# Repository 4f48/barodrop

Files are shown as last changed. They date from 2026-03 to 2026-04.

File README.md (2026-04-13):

# barodrop
A battery-powered, barometer-driven release system that automatically drops a payload at a configurable target altitude.

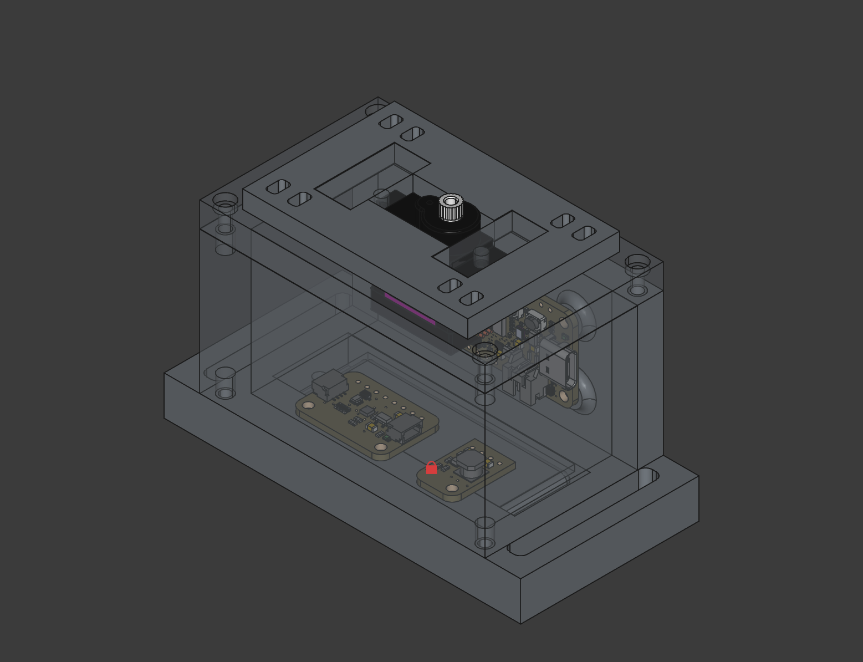
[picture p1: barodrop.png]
barodrop full assembly 3D model


## Why?
I've been participating in the Hungarian CanSat competition for two years. In my time working on the model satellite, we launched prototypes 4 times on high altitude weather balloons for testing. A key piece in these tests is the release system: it drops the CanSat before it flies too far away, making recovery marginally more difficult. However, the release system was always a pain point. Difficult to set up, integrate into existing systems' code or unreliable.

I decided to build something that solves all of these problems:

- independent electronics, keeping complexity low
- separate power supply: no battery drain
- reliability: built around a "drop plate" design
- easy setup, effortless configuration, solid construction

## Usage
Using barodrop is easy. Here's how it's done:

1. Write your desired configuration (altitude, timeout) to a microSD card and insert it into the main board.
2. Hold the flyaway part in place in order for the servo to lock it in place.
3. Plug in the battery to power on the system while holding the flyaway part.
4. Screw in the side panel.
5. You are ready to launch!

## Assembly
So you want one of these for yourself? The following guide will walk you through building it step-by-step.

### 1. Components
You'll have to source some components to build barodrop. You can find everything needed in the table below. I included the links for where I got the components.

| Component | Description | Link |
|---|---|---|
| Adafruit Feather RP2040 Adalogger | main board | [Mouser](https://mou.sr/4baPHUJ) |
| Adafruit BMP390 | barometer | [Mouser](https://mou.sr/4uvOA9I) |
| Adafruit MiniBoost 5V | booster | [Mouser](https://mou.sr/4diH9MU) |
| Tower Pro MG90S | servo motor | [HESTORE](https://www.hestore.hu/prod_10048104.html#) |
| JST PH 2-pin cable | battery cable | [Mouser](https://mou.sr/4luIpPd) |
| CNC Kitchen M2x3 | threaded insert | [3DJake](https://www.3djake.com/cnc-kitchen/threaded-inserts-m2-standard)  |
| CNC Kitchen M2.5x4 | threaded insert | [3DJake](https://www.3djake.com/cnc-kitchen/threaded-inserts-m25-standard) |
| cylinder head M2, M2.5 | screws | locally sourced / [Amazon](https://www.amazon.de/-/en/FandWay-Cylinder-Hexagon-Threaded-Stainless/dp/B0F3HJHFFS?th=1) |
| Dupont Wires | jumper wires | locally sourced / [Amazon](https://www.amazon.de/-/en/Elegoo-120pcs-Multicolored-Breadboard-arduino/dp/B01EV70C78?s=industrial&th=1) |

> Any screws (with the correct sizes) and any wires you have lying around the house will do. If you do not have any, chances are you can find these at your local hardware store. I included some Amazon links for reference.

> You can find a [more detailed BOM](https://github.com/4f48/barodrop/blob/main/BOM.csv) in the repository files.

To complete the build, you need to 3D print some parts. If you do not own a 3D printer, try a print-on-demand service. Additionally, a soldering iron with a threaded insert adapter, some solder and very basic soldering skills are needed.

### 2. Print the enclosure
Get started by 3D printing the enclosure. I recommend using PETG.

STL files: [/STL](https://github.com/4f48/barodrop/tree/main/STL)  
STEP files: [/STEP](https://github.com/4f48/barodrop/tree/main/STEP)

Print each file once. The "flyaway" part needs to be reprinted with each use, since it flies away with the balloon on release.

### 3. Insert the threads
To be able to screw the different components together, you need to install threaded inserts into the 3D printed parts.

- 2x M2 threaded inserts go into the top enclosure's bottom, near the hole in the middle.
- 1x M2 threaded insert goes into battery holder
- Populate the rest of the holes with M2.5 inserts.

### 4. Solder the components
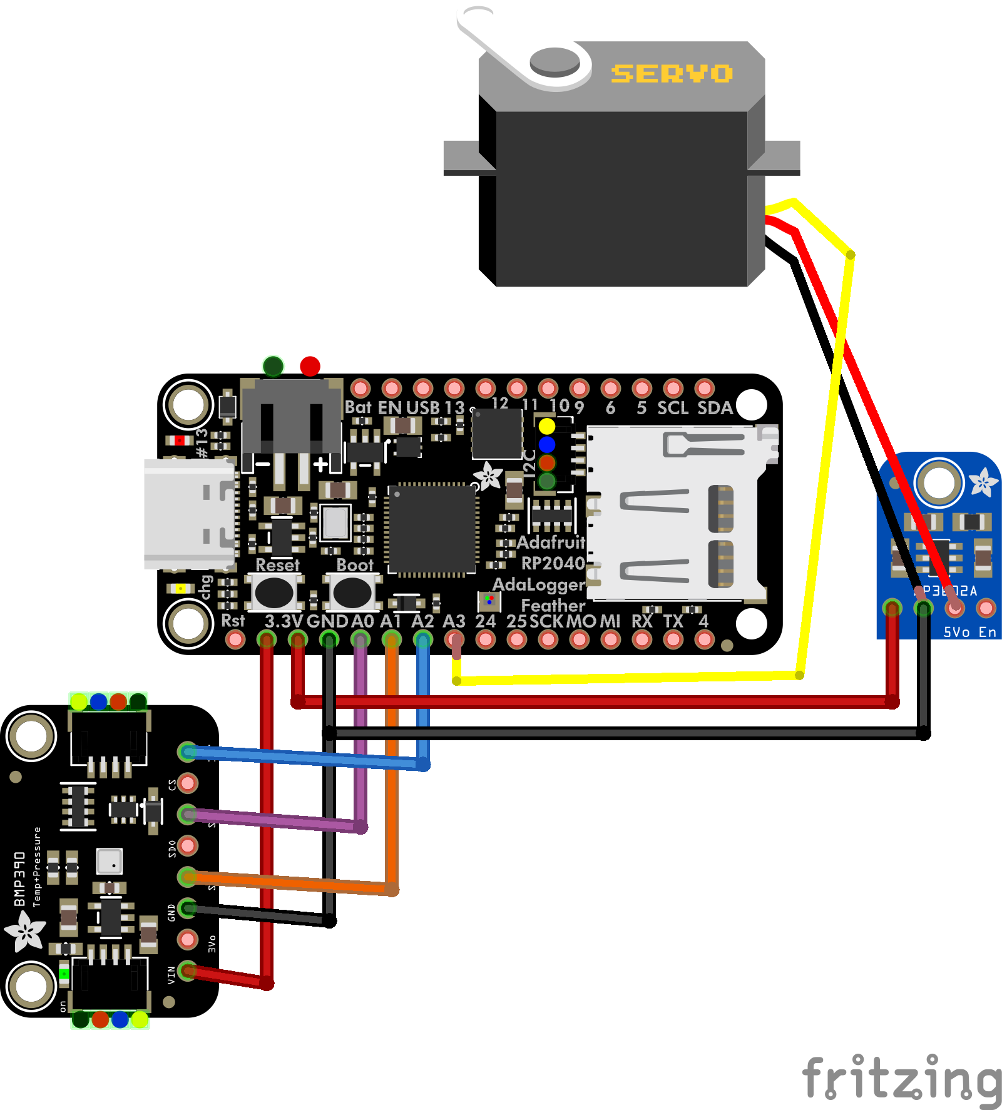
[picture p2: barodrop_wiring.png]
barodrop wiring diagram


Follow this wiring diagram to connect the components together. You might need to cut off a plug from the end of the servo's wires.

The battery comes with an incompatible connector from the factory. Cut it off, and solder on the 2-pin JST PH cable. Keep polarity in mind.

### 5. Load firmware
Firstly, download [barodrop-firmware](https://github.com/4f48/barodrop/blob/main/barodrop-firmware) from this repository.

Enter the bootloader by holding down the "Boot" button, and while continuing to hold it, press and release the "Reset" button. Keep holding the "Boot" button until the RPI-RP2 drive appears. Copy the downloaded firmware file to the RPI-RP2 drive. The RPI-RP2 drive will disappear when the firmware is loaded.

### 6. Assembly
You are almost done, we just need to put everything together. Start by placing the battery in the bottom enclosure. Cover it with the battery holder, and screw in the battery holder from the bottom. Next, mount the main board, the barometer and the booster to the bottom enclosure.

Use two M2 screws to attach the servo motor to the top enclosure. Secure the top enclosure to the bottom enclosure. Finally, screw in the side panel using two screws on the top and bottom. If you intend to power on the circuit, plug in the battery cable before screwing in the side panel.

## Bill of Materials

Download as CSV: [BOM.csv](https://github.com/4f48/barodrop/blob/main/BOM.csv)  
Download as OpenDocument Spreadsheet: [BOM.ods](https://github.com/4f48/barodrop/raw/refs/heads/main/BOM.ods)

| Component | Description | Link |
|---|---|---|
| Adafruit Feather RP2040 Adalogger | main board | [Mouser](https://mou.sr/4baPHUJ) |
| Adafruit BMP390 | barometer | [Mouser](https://mou.sr/4uvOA9I) |
| Adafruit MiniBoost 5V | booster | [Mouser](https://mou.sr/4diH9MU) |
| Tower Pro MG90S | servo motor | [HESTORE](https://www.hestore.hu/prod_10048104.html#) |
| JST PH 2-pin cable | battery cable | [Mouser](https://mou.sr/4luIpPd) |
| CNC Kitchen M2x3 | threaded insert | [3DJake](https://www.3djake.com/cnc-kitchen/threaded-inserts-m2-standard)  |
| CNC Kitchen M2.5x4 | threaded insert | [3DJake](https://www.3djake.com/cnc-kitchen/threaded-inserts-m25-standard) |
| cylinder head M2, M2.5 | screws | locally sourced / [Amazon](https://www.amazon.de/-/en/FandWay-Cylinder-Hexagon-Threaded-Stainless/dp/B0F3HJHFFS?th=1) |
| Dupont Wires | jumper wires | locally sourced / [Amazon](https://www.amazon.de/-/en/Elegoo-120pcs-Multicolored-Breadboard-arduino/dp/B01EV70C78?s=industrial&th=1) |

> Any screws (with the correct sizes) and any wires you have lying around the house will do. If you do not have any, chances are you can find these at your local hardware store. I included some Amazon links for reference.

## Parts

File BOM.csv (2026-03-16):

Part | Description | Amount | MPN | Link
Adafruit Feather RP2040 Adalogger | main board | 1 | 5980 | https://mou.sr/4baPHUJ
Adafruit BMP390 | barometer | 1 | 4816 | https://mou.sr/4uvOA9I
Adafruit MiniBoost 5V | booster | 1 | 4654 | https://mou.sr/4diH9MU
Tower Pro MG90S | servo motor | 1 | MG90S-360 | https://www.hestore.hu/prod_10048104.html
JST PH 2-pin cable | battery cable | 1 | 261 | https://mou.sr/4luIpPd
CNC Kitchen M2x3 | threaded insert | 1 | TC-M2x3,0 | https://www.3djake.com/cnc-kitchen/threaded-inserts-m2-standard
CNC Kitchen M2.5x4 | threaded insert | 1 | TC-M2,5x4 | https://www.3djake.com/cnc-kitchen/threaded-inserts-m25-standard
cylinder head M2 | screw | 3 | N/A | https://www.amazon.de/-/en/FandWay-Cylinder-Hexagon-Threaded-Stainless/dp/B0F3HJHFFS?th=1
cylinder head M3 | screw | 13 | N/A | https://www.amazon.de/-/en/FandWay-Cylinder-Hexagon-Threaded-Stainless/dp/B0F3HJHFFS?th=1
Dupont wires | jumper wires | 7 | N/A | https://www.amazon.de/-/en/Elegoo-120pcs-Multicolored-Breadboard-arduino/dp/B01EV70C78?s=industrial

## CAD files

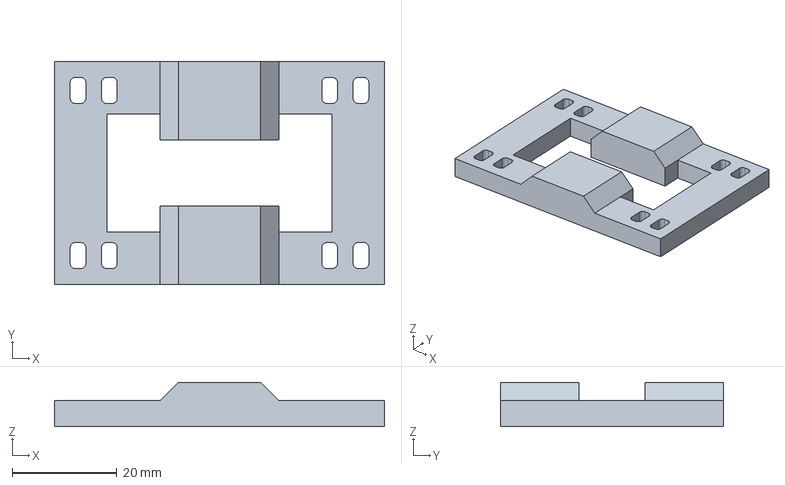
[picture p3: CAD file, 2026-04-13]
barodrop.FCStd
63.1 x 42.6 x 8.50 mm

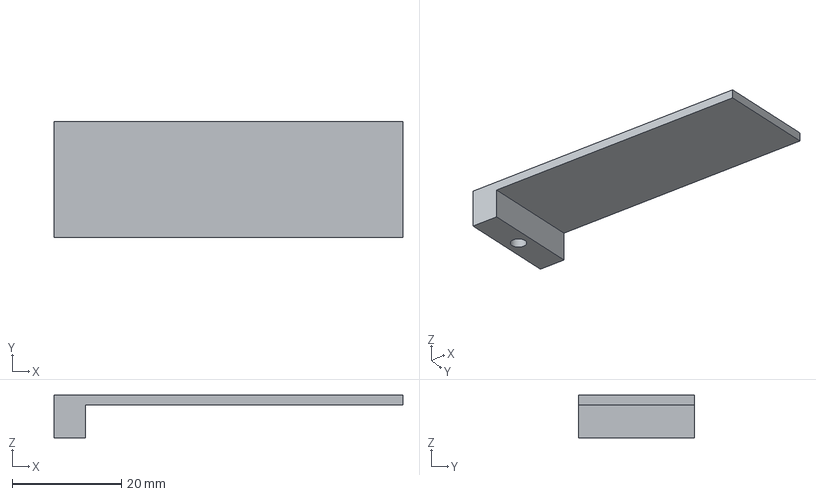
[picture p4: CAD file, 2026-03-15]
STEP/barodrop-Battery_Holder.step
63.8 x 21.2 x 7.80 mm

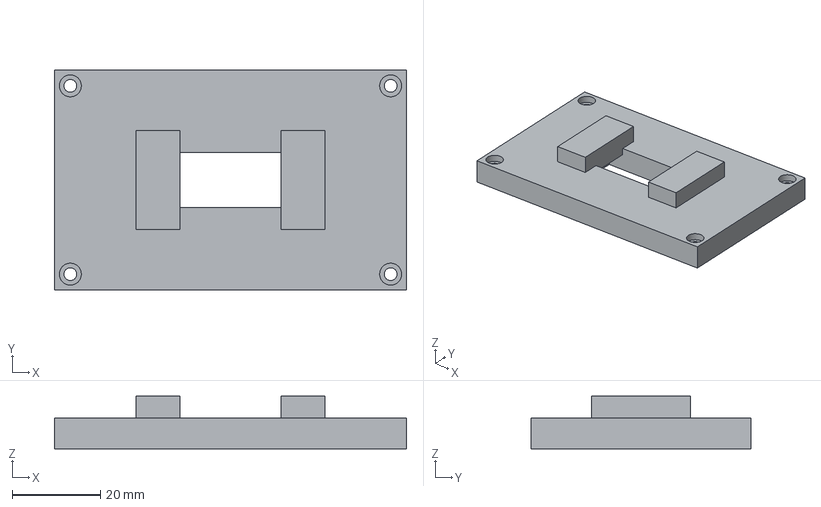
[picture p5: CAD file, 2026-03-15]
STEP/barodrop-Enclosure_Top.step
80.0 x 50.0 x 12.0 mm

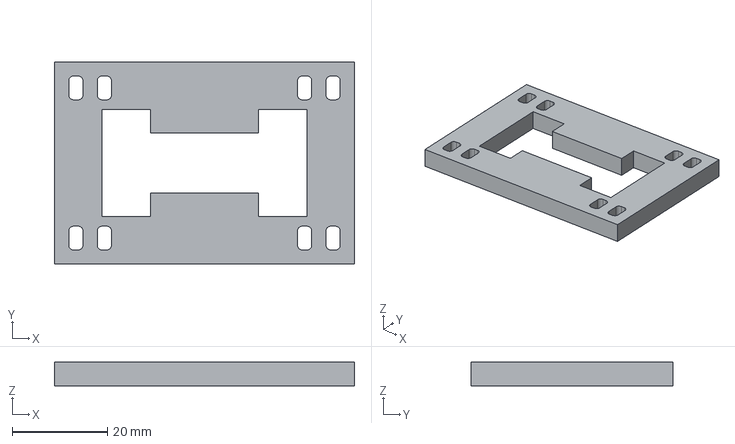
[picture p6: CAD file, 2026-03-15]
STEP/barodrop-Flyaway.step
63.1 x 42.6 x 5.00 mm

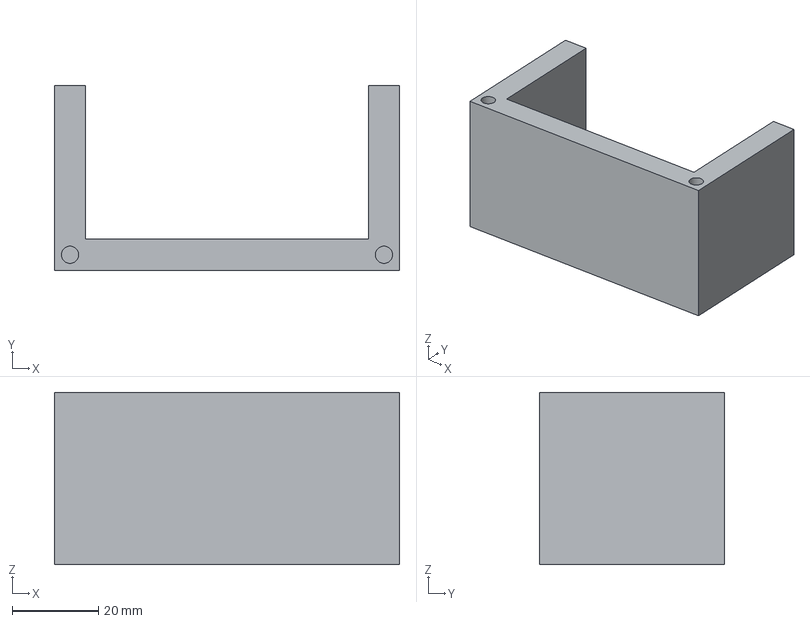
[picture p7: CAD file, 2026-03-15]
STEP/barodrop-Enclosure_Side.step
80.0 x 42.8 x 39.9 mm

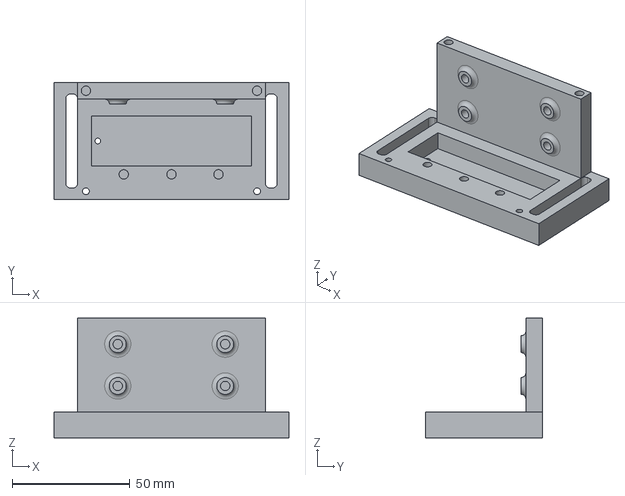
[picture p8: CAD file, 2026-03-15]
STEP/barodrop-Enclosure_Bottom.step
100.0 x 50.0 x 51.0 mm

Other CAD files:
STL/barodrop-Battery_Holder.stl
STL/barodrop-Enclosure_Bottom.stl
STL/barodrop-Enclosure_Side.stl
STL/barodrop-Enclosure_Top.stl
STL/barodrop-Flyaway.stl

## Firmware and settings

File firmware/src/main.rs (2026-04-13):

#![no_std]
#![no_main]

use bmp390_rs::{Bmp390, Interrupts, config::Configuration};
use embassy_executor::Spawner;
use embassy_rp::{
    bind_interrupts, dma,
    gpio::{Input, Output},
    i2c,
    peripherals::{DMA_CH0, DMA_CH1, I2C1, USB},
    pwm, spi, usb,
};
use embassy_time::Delay;
use embedded_io_async::Read;
use libm::powf;
use log::info;
use panic_halt as _;
use rp_servo::Servo;
use sd_fat::{
    block_device::sdcard::SdCard,
    fs::{Dir, DirEntry, FileSystem, fat32::Fat32},
};

bind_interrupts!(struct Irqs {
    USBCTRL_IRQ => usb::InterruptHandler<USB>;
    I2C1_IRQ => i2c::InterruptHandler<I2C1>;
    DMA_IRQ_0 => dma::InterruptHandler<DMA_CH0>, dma::InterruptHandler<DMA_CH1>;
});

#[embassy_executor::task]
async fn logger_task(driver: usb::Driver<'static, USB>) {
    embassy_usb_logger::run!(512, log::LevelFilter::Info, driver);
}

#[embassy_executor::main]
async fn main(spawner: Spawner) {
    let p = embassy_rp::init(Default::default());
    let usb_driver = usb::Driver::new(p.USB, Irqs);
    spawner.spawn(logger_task(usb_driver).unwrap());

    let spi = spi::Spi::new(
        p.SPI0,
        p.PIN_18,
        p.PIN_19,
        p.PIN_20,
        p.DMA_CH0,
        p.DMA_CH1,
        Irqs,
        Default::default(),
    );
    let cs = Output::new(p.PIN_23, embassy_rp::gpio::Level::High);
    let sd = SdCard::new(spi, cs).await.unwrap();
    let mut fs = Fat32::mount(sd).await.unwrap();
    let mut root = fs.open_dir("/").await.unwrap();
    let config_entry = root.find("CONFIG~1.TOM").await.unwrap();
    let mut config_file = fs.open_file_at(config_entry.cluster(), config_entry.size());

    let mut buf = [0u8; 128];
    let n = config_file.read(&mut buf).await.unwrap();

    let content = core::str::from_utf8(&buf[..n]).unwrap().trim();
    let (_, value) = content.split_once("=").unwrap();
    let target: f32 = value.parse().unwrap();

    let pwm = pwm::Pwm::new_output_a(p.PWM_SLICE6, p.PIN_12, Default::default());
    let mut servo = Servo::new(pwm, 500, 2550);
    servo.set(0).unwrap();

    let i2c = i2c::I2c::new_async(p.I2C1, p.PIN_27, p.PIN_26, Irqs, Default::default());
    let mut int = Input::new(p.PIN_24, embassy_rp::gpio::Pull::None);

    let bmp390_conf = Configuration::default()
        .enable_pressure_measurement(true)
        .enable_temperature_measurement(true)
        .iir_filter_coefficient(bmp390_rs::register::config::IIRFilterCoefficient::Coef3)
        .output_data_rate(bmp390_rs::register::odr::OutputDataRate::R0p78Hz)
        .power_mode(bmp390_rs::register::pwr_ctrl::PowerMode::Normal)
        .pressure_oversampling(bmp390_rs::register::osr::Oversampling::X8)
        .temperature_oversampling(bmp390_rs::register::osr::Oversampling::X1);
    let mut bmp390 = Bmp390::new_i2c(
        i2c,
        bmp390_rs::SdoPinState::High,
        bmp390_conf,
        bmp390_rs::ResetPolicy::Soft,
        &mut Delay,
    )
    .await
    .unwrap();
    bmp390
        .mask_interrupts(Interrupts::new().fifo_full().fifo_watermark())
        .await
        .unwrap();

    for _ in 0..3 {
        int.wait_for_rising_edge().await;
        bmp390.read_sensor_data().await.unwrap().pressure();
    }
    int.wait_for_rising_edge().await;
    let base = bmp390.read_sensor_data().await.unwrap().pressure();
    servo.set(90).unwrap();

    loop {
        int.wait_for_rising_edge().await;
        let pressure = bmp390.read_sensor_data().await.unwrap().pressure();
        let altitude = altitude(base, pressure);

        if altitude > target {
            servo.set(0).unwrap();
        }

        info!("{} / {}", altitude, target);
    }
}

fn altitude(base: f32, pressure: f32) -> f32 {
    44330.0 * (1.0 - powf(pressure / base, 0.1903))
}

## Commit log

2026-03-15 add 3d files
    [barodrop-Battery_Holder.step, barodrop-Battery_Holder.stl, barodrop-Enclosure_Bottom.step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]
2026-03-15 add assembly
2026-03-15 wiring diagram
2026-03-16 Add BOM
    [BOM.csv, BOM.ods]
2026-03-16 Fix joined cells
    [BOM.csv]
2026-03-16 Fix image path for barodrop wiring diagram
    Updated image path for the wiring diagram in the README.
2026-04-07 adapt code
    [barodrop.FCStd]
2026-04-13 update with new firmware
    [barodrop.FCStd]
